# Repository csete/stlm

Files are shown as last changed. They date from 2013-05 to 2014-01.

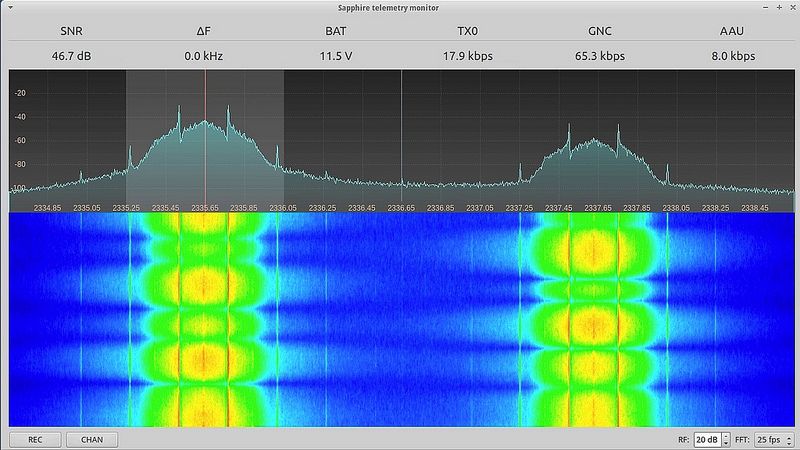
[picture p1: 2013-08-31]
doc/src/images/telemetry_monitor.jpg

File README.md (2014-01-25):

Sapphire Telemetry System
-------------------------

This repository contains the hardware and software for the Sapphire Telemetry System originally built for Copenhagen Suborbitals for their Sapphire test flight (mission video: http://www.youtube.com/watch?v=kcF5xNrb3HA).

See how the downlink performed during the test flight where the motion cause very strong fading: http://www.youtube.com/watch?v=QEViCPNmkhM

Some photos are available on Flickr: http://www.flickr.com/photos/csete/sets/72157633313520450/

The telemetry system consists of a 2.4 GHz transmitter built around the ADF7242 and a receiver built around a USRP1 with GNU Radio SDR software.

The project repository is organized in the following subdirectories:

* transmitter -- transmitter design files, including complete Eagle project and firmware source code
* receiver -- receiver design files organized as follows:
  * decoder -- The data data decoder application
  * strx -- The main GNU Radio application that acts as the software receiver
  * strx-mon -- Qt-based remote control and monitoring application for strx
  * hardware -- data sheets of varous hardware component (USRP, LNB, etc.)
* doc -- main project documentation written in asciidoc
* system -- some additional system level documentation (should also be avaialble via doc)

License and Copyright
---------------------

The transmitter is Copyright 2013 by Peter Scott, OZ2ABA.

The receiver is Copyright 2013 by Peter Scott, OZ2ABA, and Alexandru Csete, OZ9AEC.

The Viterbi decoder is Copyright Phil Karn, KA9Q,

Both the transmitter and the receiver are licensed under GNU General Public License version 3. For the transmitter other licenses can be negotiated.

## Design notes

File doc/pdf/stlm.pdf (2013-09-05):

Sapphire Telemetry System | i

# Sapphire Telemetry System

Sapphire Telemetry System | ii

REVISION HISTORY

NUMBER | DATE | DESCRIPTION | NAME
1.1 | September 2013 | | A

Sapphire Telemetry System | iii

## Contents

1 Overview | 1
2 Telemetry transmitter | 3
3 Telemetry receiver | 3
4 Packet format and bitrate budget | 11
5 Forward error correction | 13
6 Glossary | 13

Sapphire Telemetry System | 1 / 14

## 1 Overview

The Sapphire Telemetry System is a telemetry downlink system for the Sapphire test rocket by Copenhagen Suborbitals. Its purpose is to support downlink of high rate telemetry from the GNC and AAU units allowing detailed analysis of the flight.

Figure 1 shows the telemetry downlink system in context of the complete data infrastructure during the Sapphire mission. Figure 2 shows an overview of the telemetry system itself.

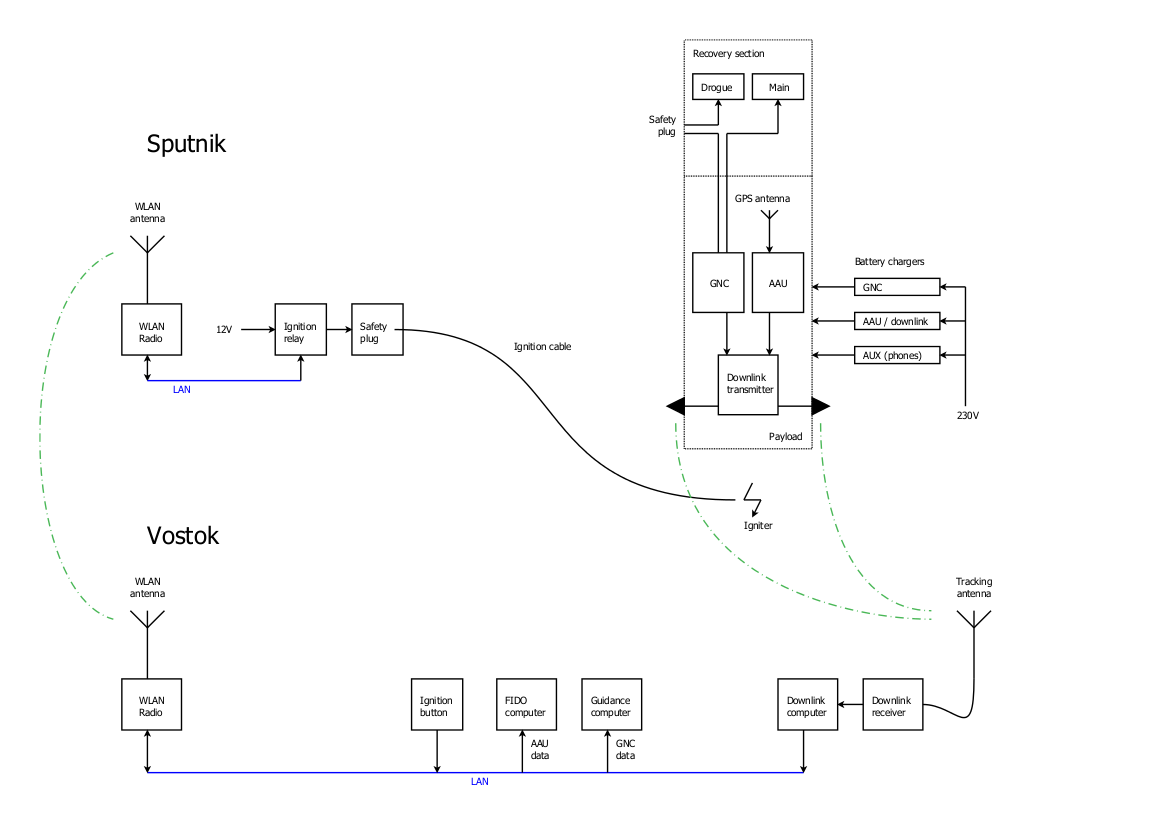
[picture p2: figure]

Figure 1: Sapphire data infrastructure

The telemetry system is based on a design originally created for the Euroluna Romit 2 cubesat and has the following character-istics:

- Two downlink channels working simultaneously.
- Works in the 13 cm amateur / ISM band.
- 1 watt RF output per channel (adjustable in firmware)
- Up to 2 Mbps bit rate per channel (including all headers, FEC, etc.)
- GFSK modulation
- CRC and FEC (rate 1/2)

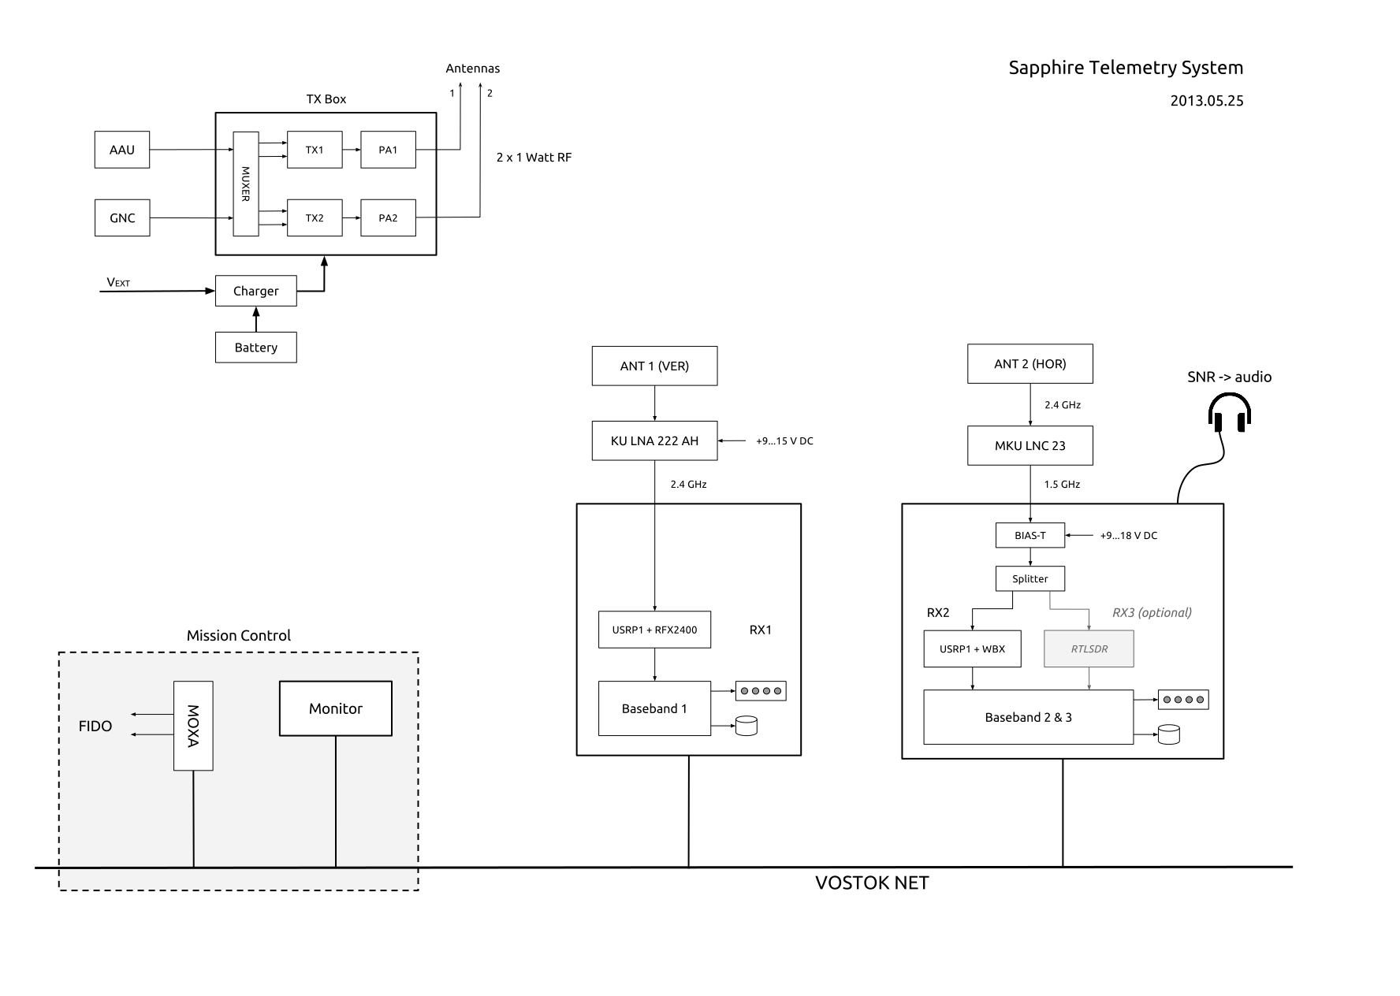
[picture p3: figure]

Figure 2: Telemetry system overview

The telemetry system contains the following components:

Transmitter
The transmitter is based on the ADF7242 transceiver chip running in raw mode. The digital data interface to the payload goes through a PIC24, which is responsible for converting the potentially variable rate data to fixed rate. The transmitter is described in more details in Section 2.

Receiver
The receiver is a software defined radio using USRP hardware and GNU Radio based software receiver. It runs on a Linux PC and delivers the telemetry data via Ethernet or RS232 interface. The receiver is set up to run autonomously and does not require any user intervention; however, key parameters are exported via a control port interface. This allows remote clients to connect to the receiver, monitor the system performance, and modify some key parameters. The receiver is described in details in Section 3.

Control panel
The monitoring and control panel is a client that connects to the receiver and displays system performance (spectrum, SNR, data and error rates, etc.) to mission control crew. It also allows modifying some basic settings in the receiver chain such as frequency, active channel, recording on/off, etc. The control panel is described in more details together with the receiver in Section 3.

Tracking tower
An AZ/EL mount built specifically for tracking fast flying objects. It can carry many antennas of different shapes and sizes as long as the construction stays balanced. For the Sapphire mission it carries two 2.4 GHz yagi antennas, one vertically and horizontally polarized. Each antenna is connected to a receiver that receives both downlink channels; however, only one channel of the horizontal receiver is monitored in real time. The other channels are recorded for reference. The tracking tower has been described in TBD.

In addition to the unit documentation listed above, following system level documentation exists:

Packet format
Describes the packet format used by the telemetry system, see Section 4.

Forward error correction
Describes the error correction code used by the system, see Section 5.

## 2 Telemetry transmitter

The transmitter is based around the ADF7242 FSK transceiver chip by Analog Devices. The transceiver is used in raw FSK mode as opposed to any of the pre-programmed modes in the chip. Raw FSK mode allows up to 2 Mbps data rate.

Figure 3: Functional diagram of the telemetry transmitter.

The transmitter is connected to the GNC and AAU unit using a serial interface. This interface is provided by a PIC24 microcon-troller which is in charge of all the data handling, including preparing the packets, calculating CRC and adding FEC. Moreover, the PIC24 is also responsible for configuring and controlling the ADF7242 transceiver chip.

For the Sapphire mission we were using 250 kbps bit rate with rate 1/2 FEC, i.e. 125 kbps data throughput. The 125 kbps data includes packet headers and other bookkeeping data. See Section 4 for details about the packet format.

The ADF7242 transmitter is running in GFSK mode. This eliminates the minimum shift restriction of FSK and reduces the occu-pied bandwidth (the transmitter uses 260 kHz shift in our case). On the other hand this also introduces inter-symbol interference that must be compensated for at the receiver end.

The ADF7242 transceiver chip is followed by a low pass filter, an ABA-54563 buffer amplifier and finally an ALM-31222 power amplifier capable of delivering 1W RF into the antenna.

## 3 Telemetry receiver

The Sapphire telemetry receiver is based on a Universal Software Radio Peripheral (USRP) hardware from Ettus Research and the GNU Radio software defined radio framework.

As indicated on Figure 2 in Section 1 we designed the system to use three receiver chains running parallel. One for receiving each telemetry channel using a USRP and a third one for testing and RTL-SDR receiver. Due to time constraints, we ended up using one USRP-based receiver for real time reception and one USRP-based receiver for recording the I/Q data to disk. The RTL-SDR experiment was not performed.

Figure 4 below shows an overview of the receiver used for real time reception.

Figure 4: Sapphire telemetry receiver

It uses an MKU LNC 23 down-converter from Kuhne Electronic, a USRP1 equipped with a WBX transceiver daughter card and connected to a PC running software receiver and data decoder. Each of these components are described in the following sections.

### 3.1 MKU LNC 23 down-converter

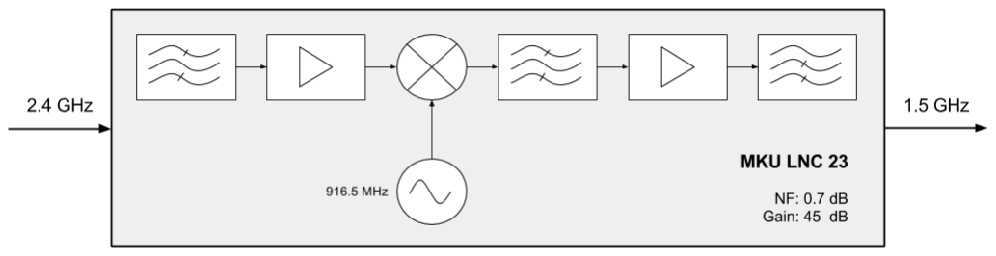
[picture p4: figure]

Figure 5: Kuhne MKU LNC 23 down-converter

The MKU LNC 23 (http://www.kuhne-electronic.de/en/products/down-converters/mku-lnc-23.html) down-converter from Kuhne Electronic (http://www.kuhne-electronic.de/startseite.html) is mounted directly on the antenna and connected using a very short coaxial cable. This gives the primary receiver chain a low noise figure and provides sufficient gain to run a long coax cable down to the receiver, which is located below deck.

The down-converter has built-in bias tee and is supplied through the coax. The supply voltage is injected into the coax using a bias tee at the USRP end below the deck.

### 3.2 USRP with WBX front end

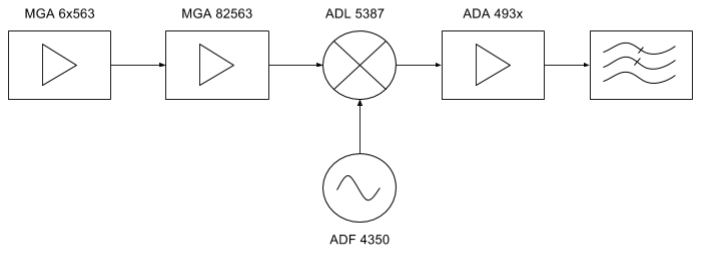
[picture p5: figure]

Figure 6: WBX receiver

The WBX transceiver board covers 50 MHz to 2.2 GHz and it has one of the best performing receivers for the USRPs. Figure 6 shows a high level diagram of the receiver part.

The board has two amplifier stages (MGA62563 and MGA82563) followed by the ADL5387 quadrature demodulator. The analog I/Q goes through an ADC driver and an anti alias filter with cut-off at around 50 MHz before it is routed to the ADC on the USRP main board.

Figure 7: USRP1 receiver

The ADC on the USRP1 runs at 64 MHz and could theoretically provide 64 MHz of bandwidth. However, since the USRP1 is connected to the host PC through USB2, the usable real-time bandwidth is limited to 8 MHz at 16 bit resolution. To that end, the ADC is followed by an FPGA running a digital down converter (DDC) providing a means to convert the 64 MHz to a lower rate. The USRP1 supports a wide variety of sample rates between 250 kHz and 8 MHz. For the Sapphire mission we have been using 4 MHz bandwidth allowing us to monitor both transmitters at the same time.

Schematics of the USRP1 and the WBX RF board are included in the receiver/hardware/ (https://github.com/csete/stlm/tree/master/receiver/hardware) directory.

### 3.3 Software receiver

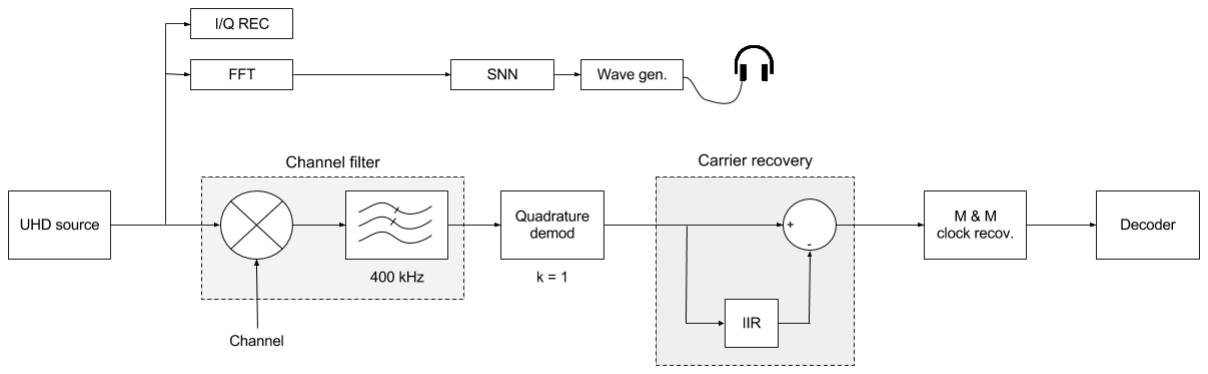
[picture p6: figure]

Figure 8: GNU Radio software receiver

The software receiver is a C++ application built using the GNU Radio SDR framework. The receiver uses both DSP blocks and the run-time framework provided by GNU Radio. In addition to that, the telemetry receiver also takes advantage of the control port interfaces, which is one of the latest additions to GNU Radio.

Most of the signal processing is executed by the GNU Radio scheduler and runs within that context. There are a few exceptions, namely the FFT block and the SNN calculations. These blocks are run in a separate boost thread scheduled periodically at 25-50 Hz. Since these are user interface related processing, there is no need to run them at higher rates.

### 3.3.1 Signal processing blocks

UHD source

The UHD source block provides the interface to the USRP hardware. We chose to use gr-uhd as input source for the Sapphire mission because we only needed USRP interface. A gr-osmosdr source could be used instead with minor modifications.

FFT

This blocks performs complex FFT on the input spectrum. The FFT is performed in three stages: 1. The first stage is a block in the GNU Radio flow graph that stores the incoming samples in a circular buffer. 2. The second stage fetches the last N samples from the circular buffer (N is the FFT size), performs the FFT calculations and prepares the data for presentation (scales to dBFS and translates the spectrum). This function is executed periodically at 25-50 Hz outside of the GNU Radio scheduling. 3. The third stage delivers the latest FFT data to external clients through the gnuradio-controlport interface.

I/Q recorder

This block is a simple file sink that dumps the complex I/Q samples to a file.

We found that it is rather problematic to save I/Q files at high rate and perform real time signal processing at the same time on the same computer. When recording is enabled, the operating system will start caching until it runs out of available RAM. Once it’s out of RAM it will start writing data to the disk periodically. The amount of data that needs to be written is huge and SDR processing is suspended during the write. Although the dropouts are very brief in duration, they are quite frequent and lead to loss of samples. Consequently, the correctly received packet rate dropped from 99% to 60%.

There are several things one can do to improve the situation:

1. Use faster hardware optimized for continuous disk I/O.
2. Get more RAM and use a RAM disk if possible. This can’t be used for long duration recordings.
3. Tune the virtual memory parameters of the kernel. We found that following parameters allowed for continuous recording on a low end Dell server:

sysctl -w vm.swappiness=0
sysctl -w vm.dirty_background_bytes=1048576 sysctl -w vm.dirty_writeback_centisecs=20 sysctl -w vm.dirty_expire_centisecs=30

The above settings pretty much disables caching and are not recommended for daily use on desktop systems. Use "vmstat 1" for monitoring how the system is caching. Documentation for the Linux kernel VM settings is available in the sysctl/vm document. (https://www.kernel.org/doc/Documentation/sysctl/vm.txt)

SNN & tracking

The SNN block calculates the (S+N)/N ratio where S stand for signal power and N for noise power in dB. The SNN is converted to an audio tone by the wave generator block and is used as an audio aid for tracking. The higher the tone the stronger the signal.

The SNN calculation is based on the FFT. Therefore, the SNN and wave generator blocks are scheduled by the same thread as the FFT processing outside of the GNU Radio main loop.

Frequency translating FIR filter

The frequency translating FIR filter has three functions:

1. Translate the spectrum so that the signal of interest is at 0 Hz.
2. Perform low pass filtering.
3. Decimate the data to a lower rate.

The frequency translation allows us to perform software-based tuning within the received spectrum. We use this functionality to select which downlink channel to decode i real time, see e.g. Figure 11.

The cut-off frequency of the low pass filter is initially set to 400 kHz but it can be adjusted during run time. The transition width is set to be equal to the cut-off frequency. Note that a 400 kHz cut-off corresponds to an 800 kHz wide channel when we are filtering at complex baseband.

The decimation factor is set to 2 so the spectrum after the filter is 2 MHz wide.

Demodulator

The transmitter uses frequency shift keying followed by a Gaussian filter to eliminate the minimum shift requirement and reduce the bandwidth. On the receiver end we can use a standard quadrature demodulator followed by a matching filter to compensate for some of the inter-symbol interference introduced by the Gaussian shaping of the signal.

The quadrature demodulator block takes a parameter, which determines the modulation factor. Sometimes it’s called sensitivity, sometimes it’s called gain — we just call it k. In an analog system k is the ratio between the quadrature rate and the maximum deviation (and reversed for the modulator). In a digital system this translates to samples per symbol assuming that the minimum shift condition is met.

For the Sapphire mission we have used k = 1, which is not optimal but sufficient thanks to the large margin we had in the link budget.

FIXME: Gaussian filter is missing in the Sapphire receiver.

Carrier recovery

Under optimal conditions the output from the quadrature demodulator will be ±1 corresponding to 0 and 1. One of these optimal conditions is that the receiver is tuned to the exact same frequency as the transmitter. In practice this is rather difficult and expensive to accomplish and it is better to tolerate slight frequency offsets.

When using frequency modulation such an offset will cause the output levels from the demodulator to shift up or down by a constant and is therefore easy to compensate. We use a single pole IIR filter to calculate the running average of the output samples and correct for the offset before sending the samples to the clock recovery block. This has the advantage of being able to correct even for variable frequency drifts.

For the Sapphire mission we used alpha = 1e-3, corresponding to a time constant 0.5 ms.

Clock recovery

Our sample rate after the channel filter is reduced to 2 Msps. With a symbol rate of 250k this gives us 8 samples per symbol to work with. However, clock skew between the transmitter and the receiver may lead to this rate being different in practice, e.g. 7.998 or 8.01. The clock recovery block helps us determine this clock skew and select the "best" sample to be sent to the decoder.

The Mueller & Muller clock recovery algorithm requires only one sample per symbol and finds the correct timing by calculating an error term using the present and the previous symbol:

en = (y’n * yn-1) - (yn * y’n-1)

where y refers to the symbol (+1 or -1) and y’ refers to the actual sample (any float).

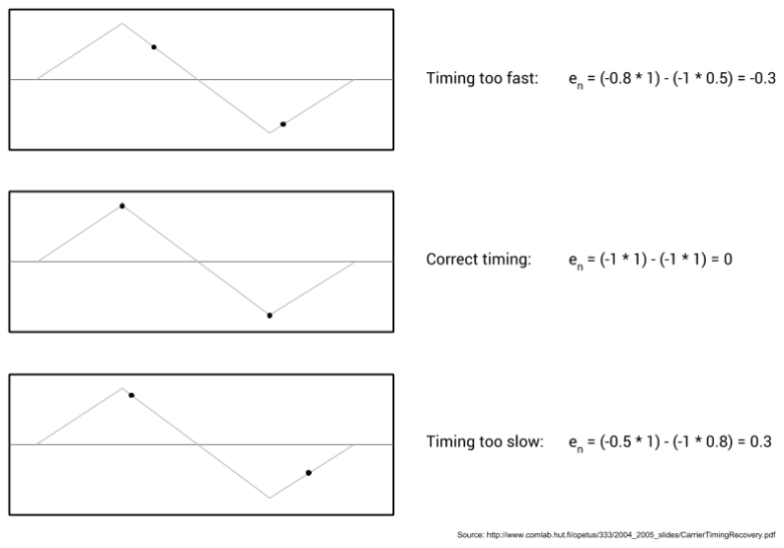
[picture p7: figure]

Figure 9: Mueller & Muller clock recovery

The Mueller & Mullerr clock recovery algorithm is sensitive to carrier offsets which is why we perform the carrier recovery described in the previous section.

### 3.3.2 Command line interface

The software receiver is a command line application with the following command line options:

alc@atlantis:~/sdr/stlm.git/receiver/build$ ./strx -h
linux; GNU C++ version 4.7.3; Boost_105300; UHD_003.005.003-140-gc099f2b5

Sapphire telemetry receiver 0.3
Command line options:
-h [ --help ] | This help message
-n [ --name ] arg | Receiver name (used for ctrlport)
-i [ --input ] arg | USRP sub device or I/Q file (use file:/path/to/file)
-a [ --ant ] arg | Select USRP antenna (e.g. RX2)
-f [ --freq ] arg | RF frequency in Hz or using G, M, k suffix
-g [ --gain ] arg | RF/IF gain in dB
-l [ --lnb ] arg | LNB LO frequency in Hz or using G, M, k suffix
-o [ --output ] arg | Output file (use stdout if omitted)
--audio arg (=none) | Audio output device (e.g. pulse, none)

### 3.4 Data decoder

Figure 10: Data decoder

The data decoder runs as a separate process

First, the decoder looks for the sync bytes that each packet begins with c.f. Figure 12 in Section 4. Once sync is obtained the decoder begins running the bytes through the Viterbi decoder. Recall that we are using convolutional FEC and all bytes in a FEC frame are encoded.

The final step in the decoding process is the packet recovery, which consists of detecting the packet boundary, checking the packet length, the CRC, extracting the packet source and finally forwarding it to the respective user.

### 3.5 Monitoring and control


Figure 11: Sapphire telemetry monitor

Monitoring and control of the receiver is carried out using the Sapphire telemetry monitor. It is a simple Qt-based application called strx-mon, which connects to the receiver and the data decoder using network sockets.

Connection to the receiver is done through the gnuradio-controlport interface. Following interfaces are implemented for the Sapphire mission:

- FFT and waterfall plot of the receiver spectrum (4 MHz).
- Change FFT rate.
- Toggle between downlink channels.
- Signal to noise ratio (SNN actually) of the selected channel.
- Show and adjust filter bandwidth.
- Show and adjust USRP gain.
- Start and stop I/Q recording.

Connection to the data decoder is done through a raw TCP connection. Whenever a character is sent over the connection, the decoder will reply with:

- Decoded AAU telemetry in bytes.
- Decoded GNC telemetry in bytes.
- Decoded transmitter telemetry in bytes.

- Current transmitter ID.
- Current battery voltage.
- Transmitter uptime.

The telemetry monitor polls the decoder periodically and translates the received status into data throughput in kilobits per second.

You can watch the Sapphire telemetry monitor i action in this YouTube video (http://www.youtube.com/watch?v=QEViCPNmkhM) showing a replay of the data downlink during the flight. The video is also a good demonstration of the telemetry system performance under harsh flight conditions (strong vibrations and tumbling).

## 4 Packet format and bitrate budget

The Sapphire telemetry is a continuous stream of packetized data. The data comes from the GNC and AAU units and packed into the frame structure described here. When neither GNC nor AAU are transmitting data, the transmitter will fill out the empty slots using own telemetry. This will ensure that the receiver can stay locked and synchronized to the signal even when there is no telemetry from the payload.

The Sapphire telemetry system uses a very simple packet format shown on the figure below:

Figure 12: The Sapphire packet structure

A packet consists of the following parts:

- A fixed length packet header (11 bytes)
- Variable length data field (up to 255 bytes)
- CRC for the data field (2 bytes)
- FEC field that applies to parts of the header (last 5 bytes), the data field and the CRC

### 4.1 Packet header

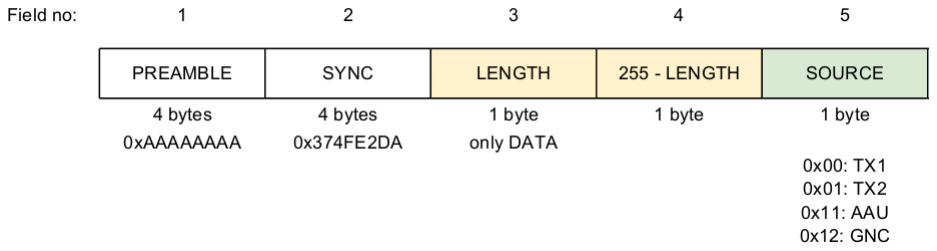
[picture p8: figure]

Figure 13: Sapphire telemetry packet header

The packet header contains the following fields:

1. A 4 byte PREAMBLE field consisting of alternating 0 and 1. The preamble is used for training the clock recovery in the receiver.
2. A 4 byte SYNC field containing the pattern 0x374FE2DA. The SYNC field is used by the correlator in the receiver to identify a packet.
3. A 1 byte LENGTH field specifying the number of bytes in the data field.
4. Another 1 byte length field but this time the "inverse" (255-LENGTH).
5. A one byte SOURCE field specifying the origin of the packet. This information is used by the data distribution system in mission control to route the packets to their respective users. Following values are valid:
- 0x00: TX1
- 0x01: TX2
- 0x11: AAU
- 0x12: GNC

### 4.2 Data field

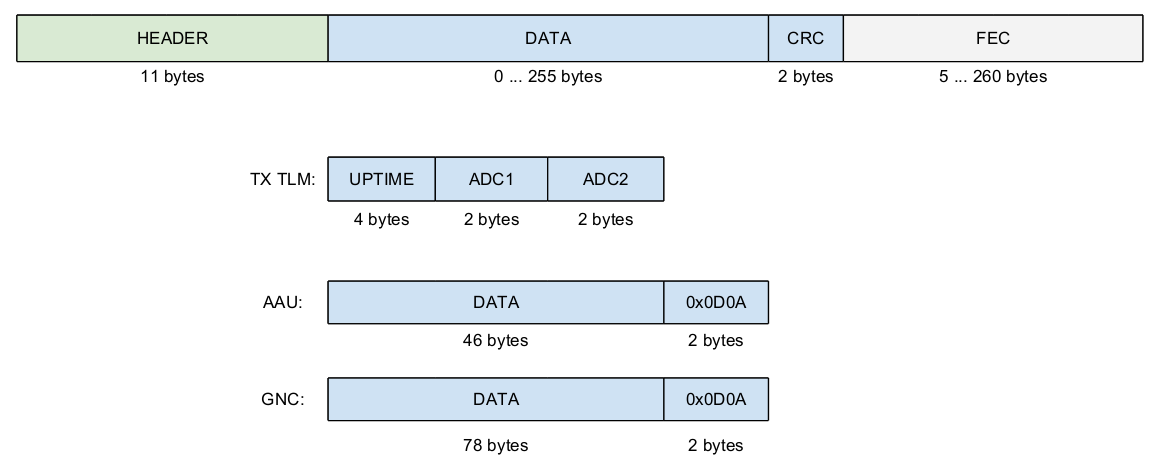
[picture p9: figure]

Figure 14: Sapphire telemetry data field

The data field contains the data as received from the payload. There are two types of payload data as indicated on the figure above. They are terminated with carriage return and linefeed characters 0x0D0A indicating packet end. The transmitter interprets this as a "flush the buffer" command even if 0x0D0A occurs inside the data. In practice this may lead to fragmentation of payload packets; however, this is not expected to cause any problems at the receiving end.

A third type of packet contains telemetry from the transmitter itself. These packets are used to fill out empty slots that are not used by the payload. See Section 4.5 for details.

The transmitter packets contain the transmitter uptime in 1/10th of a second and two raw ADC readings corresponding to the supply voltage and the temperature inside the PIC24.

### 4.3 CRC field

A 16-bit CRC is added to each packet in order to allow verifying correct packet reception. The CRC is generated using the programmable CRC generator in the PIC24 using the polynomial x¹⁶+x¹²+x⁵+1.

### 4.4 FEC field

Figure 15: FEC frame

FEC is applied to all fields except the PREAMBLE and SYNC fields in the header. A FEC frame is thus 5 + N bytes long, where N is the length of the data field. Since we are using convolutional code we do not really have separate data and FEC fields as suggested by the figure. Instead, each byte is encoded as soon as it arrives and the coded data is put into the output buffer.

### 4.5 Downlink budget

In the present configuration we have 250 kbps at our disposal. We apply rate 1/2 FEC to the data, thus we have 125 kbps at our disposal. Table 1 below shows the downlink budget under these circumstances. As can be seen from the table, almost half of the traffic is transmitter telemetry to fill out empty slots, thus there is plenty of room for future increase in data rate.

Table 1: Bitrate budget

Source | Packet size [bytes/pkt]
Packet
overhead
[bytes/pkt]

Packet
length
[bits/pkt]

Packet rate
[pkt/sec]

Bitrate [bps]

GNC | 80 | 12 | 736 | 102.25 | 75255.62
AAU | 48 | 12 | 480 | 20.00 | 9600.00
TX | 10 | 12 | 176 | 198.00 | 34848.00
Total | | | | | 119.70 k

## 5 Forward error correction

To be written

As writen in the Packet Format section, we use both CRC and rate 1/2 convolutional error correction code. While the convolutional code is used to correct bit errors in the received data, the CRC is used to verify that the received data is correct.

## 6 Glossary

AAU | Autonomous Abort Unit
ADC | Analog to digital converter
AZ | Azimuth
CRC | Cyclic redundancy check

EL | Elevation
FEC | Forward error correction
FSK | Frequency shift keying
GNC | Guidance, navigation and control
ISM | Unlicensed frequency bands used by industrial, scientific and medical devices
RF | Radio frequency
SDR | Software defined radio
SNN | Signal+noise to noise ratio
SNR | Signal to noise ratio
USRP | Universal Software Radio Peripheral

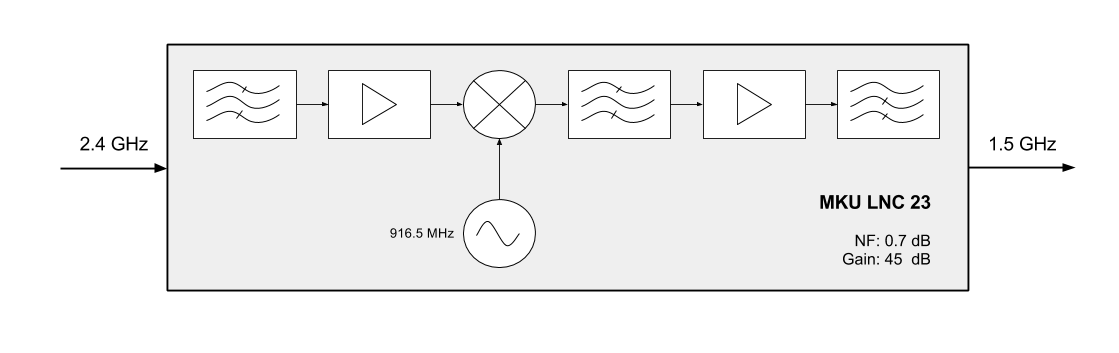
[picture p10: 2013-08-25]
doc/src/images/mku_lnc_23.png

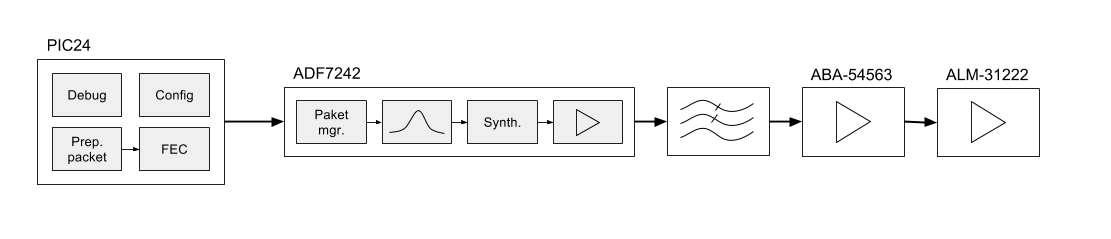
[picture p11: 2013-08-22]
doc/src/images/transmitter.png

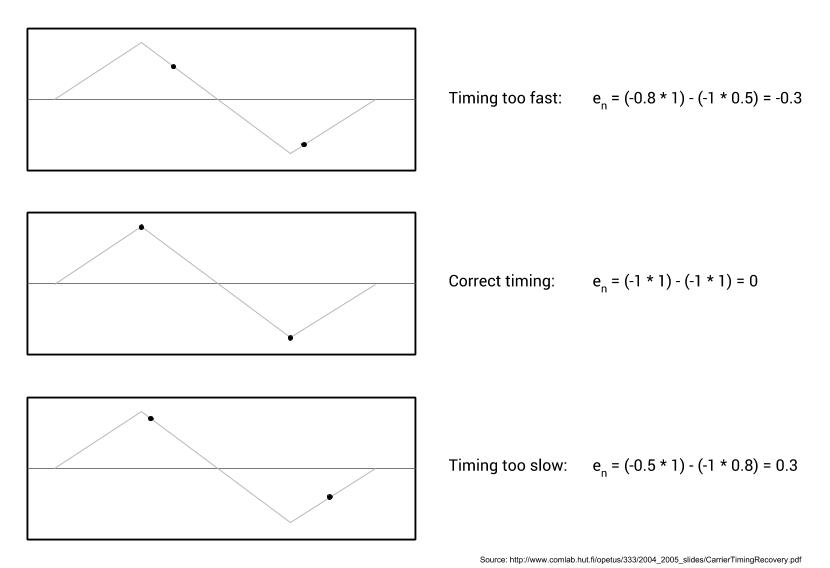
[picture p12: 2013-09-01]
doc/src/images/mm_clock_recovery.png

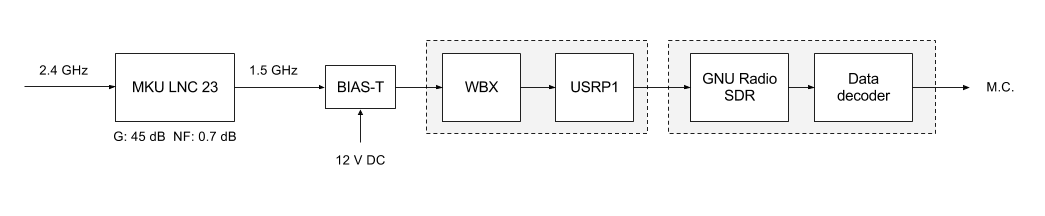
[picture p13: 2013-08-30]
doc/src/images/telemetry_receiver.png

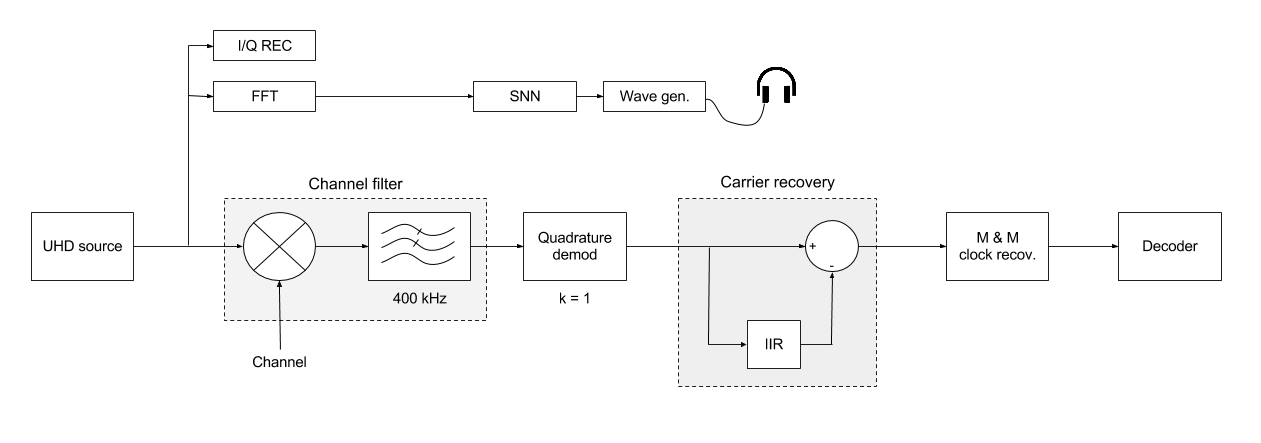
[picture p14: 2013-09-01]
doc/src/images/software_receiver.png

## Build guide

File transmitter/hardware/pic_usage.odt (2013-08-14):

Usage of PIC hardware resources

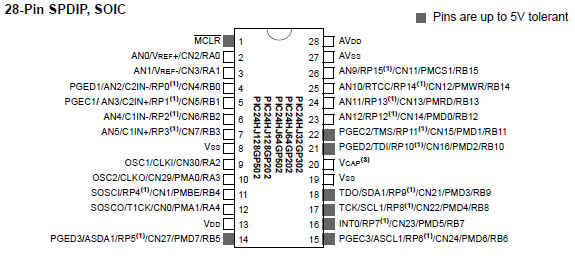
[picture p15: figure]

PIC Pin mapping

Description | PIC24 pin | | PIC24 pin | Description
-MCLR / ICSP Reset | 1 | | 28 | AVDD – 3.3 volt
RA0 - DS18 temp | 2 | | 27 | AVSS – GND
RA1 - -CS | 3 | | 26 | AN9 - Vbatt
RP0 – MOSI | 4 | | 25
RP1 – SCLK | 5 | | 24 | RP13 – RX2
RP2 – MISO | 6 | | 23 | RP12 – TX2
RP3 – TRCLK | 7 | | 22 | PGEC2 – ICSP Clock
Vss – GND | 8 | | 21 | PGED2 – ICSP Data
RA2 - LED1 | 9 | | 20 | Vcap
RA3 - LED2 | 10 | | 19 | Vss – GND
RP4 – DT | 11 | | 18 | SDA1 - I2C
RA4 - -PAenable | 12 | | 17 | SCL1 - I2C
Vdd – 3.3 volt | 13 | | 16 | RP7 - RX1
RP5 – DR | 14 | | 15 | RP6 - TX1

ADF7242 digital IO pins

Seen from top to bottom as they approach the PIC:

Pin # | Name | Function
24 | -CS | SPI Chip Select
23 | MOSI | SPI Serial Input
22 | SCLK | SPI Clock Input
21 | MISO | SPI Serial Output
19 | TRCLK_CKO_GP3 | SPORT Bit Clock Output
17 | DT_GP1 | SPORT Transmit Data Input
16 | DR_GP0 | SPORT Receive Data Output

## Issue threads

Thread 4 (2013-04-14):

LED indicator

csete, 2013-04-14:
We need a hardware indicator that can tell us the status of the complete telemetry chain. The idea is to have 4 (maybe 5) LEDs indicating the following:
- PWR: Goes on as soon as device is powered.
- RX: Goes on as soon as SNR is above threshold, which is TBC.
- SYNC: Goes on when the correlator detects valid packets.
- DATA: Goes on when the correlator detects packets from GNC or AAU.

Optionally:
- NET: Goes on when correlator successfully delivers packets to FIDO.

The easiest and fastest is probably to use an Arduino driven over usb-serial.

This works only for a single receiver and correlator, however, if the two-channel diversity is handled by the correlator, this indicator will work without modifications.

Closed 2017-03-28.

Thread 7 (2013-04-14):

Control panel

csete, 2013-04-14:
The control panel is a graphical interface to the telemetry receiver. It's purpose is to monitor the performance of the telemetry chain. The control panel does not perform any computationally intensive tasks but it must be able to perform basic graphics very efficiently.

The control panel is a client to the control port interface exposed by the telemetry receiver.

Expected hardware configuration:
- Raspberry Pi running Raspbian wheezy 2013-02-09.
- Lilliput 5D-ii/O/P 7" HDMI field monitor.
- An extension box that adds a few buttons and knobs for function shortcuts.

The control panel will organize the available parameters according to the following operating modes:
1. Mission
2. Engineering
3. Debug (TBC)

Closed 2017-03-28.

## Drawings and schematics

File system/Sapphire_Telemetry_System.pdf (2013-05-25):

## Sapphire Telemetry System

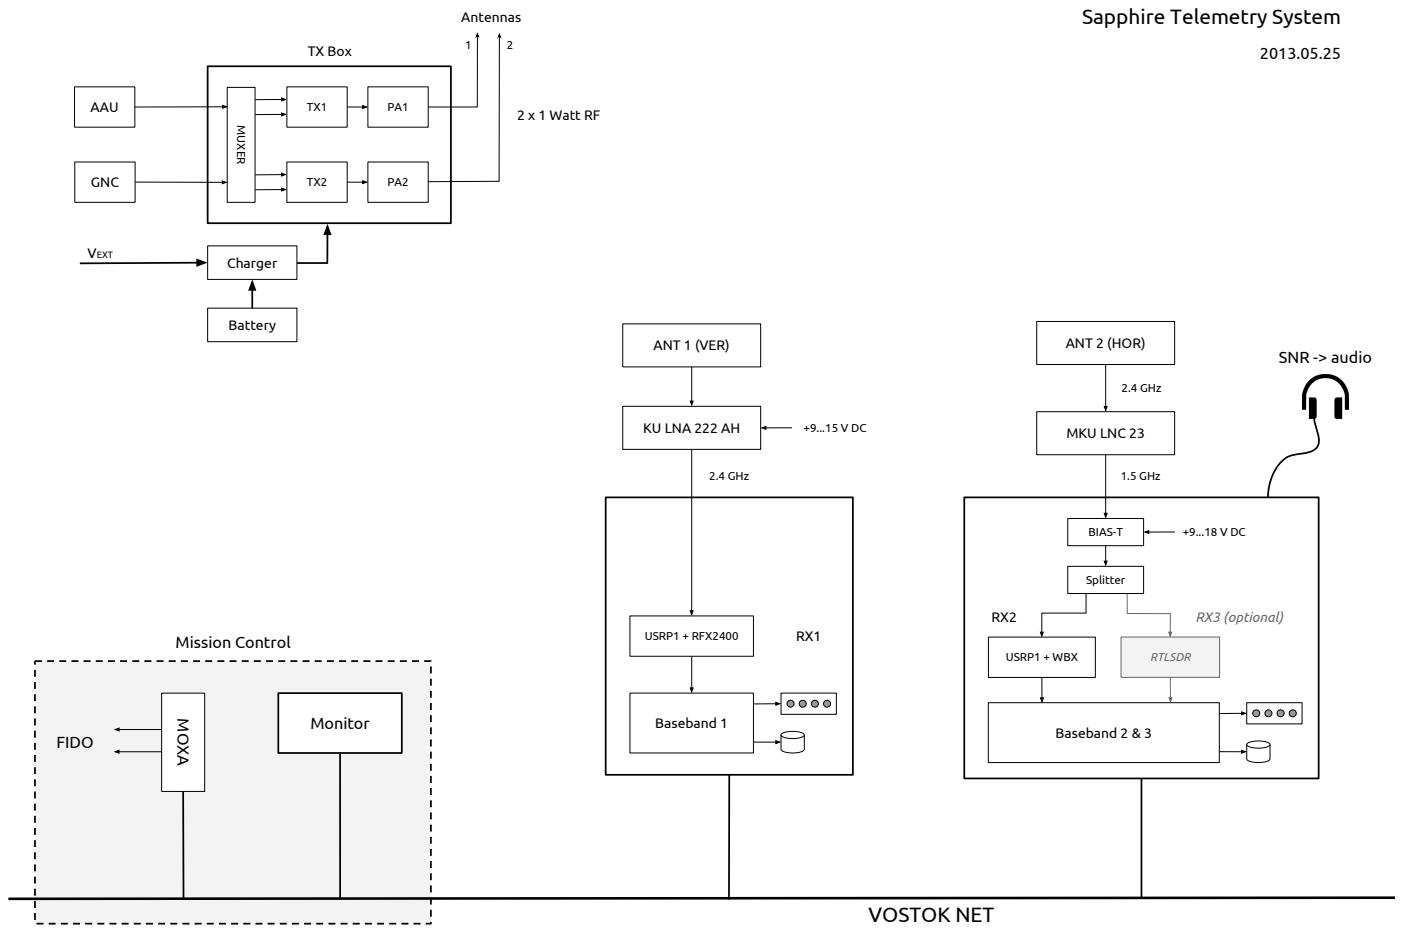
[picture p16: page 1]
AAU; GNC; MUXER; TX Box; Antennas; Charger; Battery; USRP1 + RFX2400; Baseband 1; RTLSDR; Baseband 2 & 3; RX3 (optional); Splitter; USRP1 + WBX; BIAS-T; MKU LNC 23; 1.5 GHz; 2.4 GHz; ANT 1 (VER); ANT 2 (HOR); VOSTOK NET; MOXA; Monitor; Mission Control; FIDO; KU LNA 222 AH; 2 x 1 Watt RF; VEXT; SNR -> audio

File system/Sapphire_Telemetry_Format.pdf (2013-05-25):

Field no: | 1 | 2 | 3 | 4 | 5 | 6 | 7 | 8
| PREAMBLE | SYNC | LENGTH | 255 - LENGTH | SOURCE | DATA | CRC | FEC
| 4 bytes | 4 bytes | 1 byte | 1 byte | 1 byte | up to 255 bytes | 2 bytes | 5 + LENGTH bytes
| 0xAAAAAAAA | 0x374FE2DA | only DATA | | | | | Applies to fields 3 to 7
| | | | | 0x00: TX1 0x01: TX2 0x11: AAU 0x12: GNC
TX TLM: | UPTIME | ADC1 | ADC2
| 4 bytes | 2 bytes | 2 bytes
AAU: | DATA | 0x0D0A
| 46 bytes | 2 bytes
GNC: | DATA | 0x0D0A
| 78 bytes | 2 bytes

Sapphire Telemetry Format - Overview

## Bitrate budget

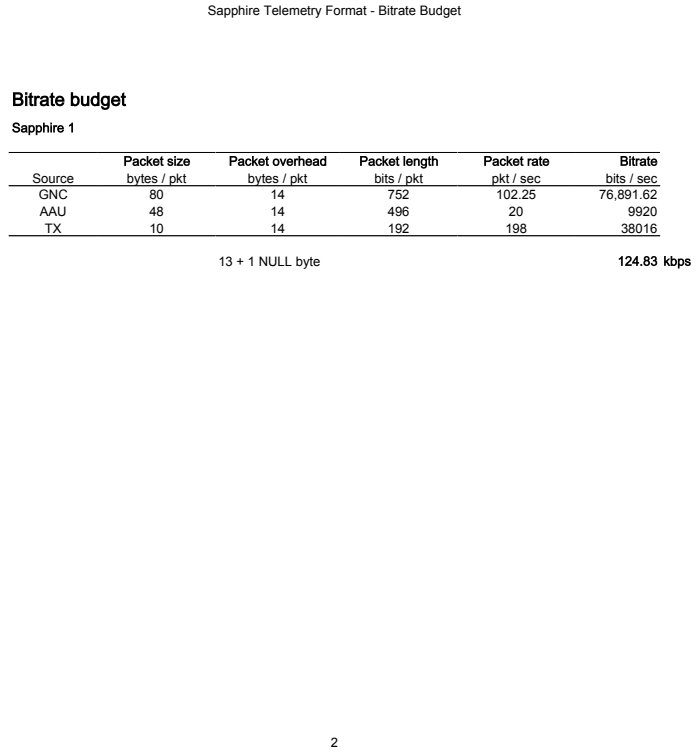
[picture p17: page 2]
13 + 1 NULL byte; kbps

Sapphire Telemetry Format - Bitrate Budget

Sapphire 1

Packet size | Packet overhead | Packet length | Packet rate | Bitrate

Source | bytes / pkt | bytes / pkt | bits / pkt | pkt / sec | bits / sec
GNC | 80 | 14 | 752 | 102.25 | 76,891.62
AAU | 48 | 14 | 496 | 20 | 9920
TX | 10 | 14 | 192 | 198 | 38016

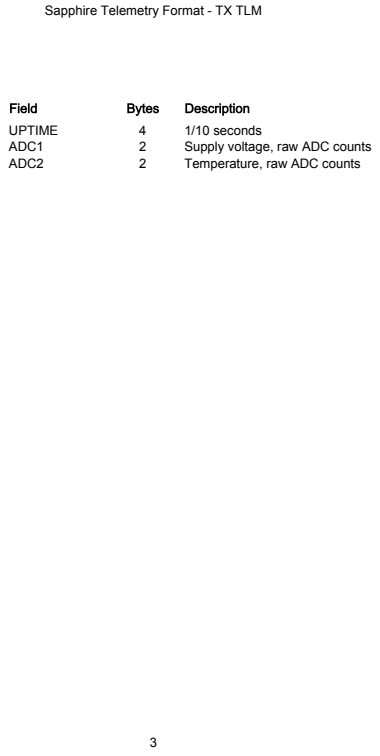
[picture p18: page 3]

Sapphire Telemetry Format - TX TLM

Field | Bytes | Description
UPTIME | 4 | 1/10 seconds
ADC1 | 2 | Supply voltage, raw ADC counts
ADC2 | 2 | Temperature, raw ADC counts

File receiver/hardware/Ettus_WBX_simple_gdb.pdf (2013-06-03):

# TX/RX

# TX_CONN6V_TX:1

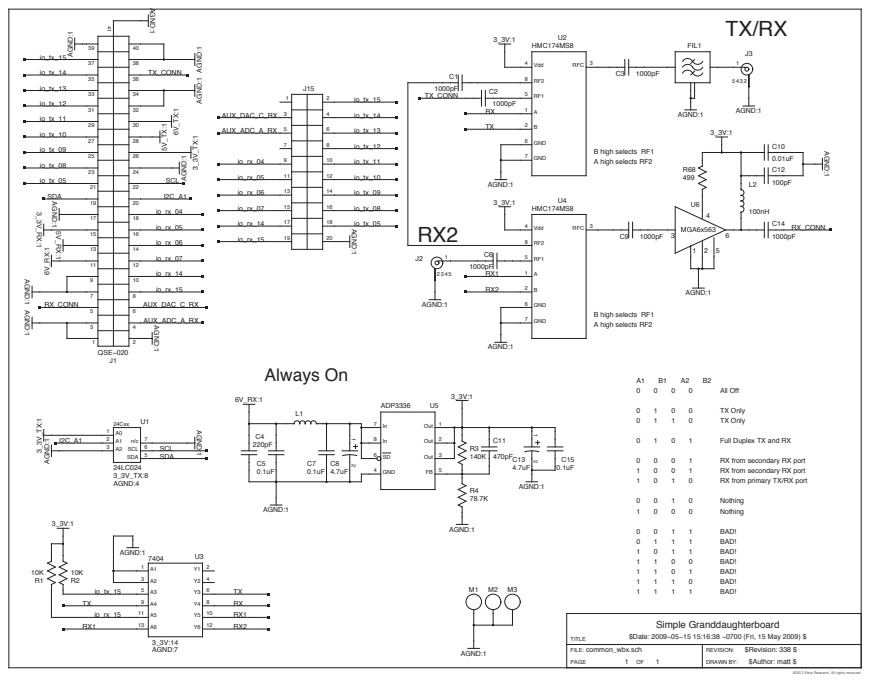
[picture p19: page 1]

©2012 Ettus Research. All rights reserved.

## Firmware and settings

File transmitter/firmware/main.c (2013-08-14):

/********************************************************************************
*																				*
*	Copenhagen Suborbitals														*
*																				*
*	2.3 GHz Telemetry Transmitter												*
*																				*
*	Version:	1.1.1															*
*	Supports hardware version 1.0 and 1.1										*
*																				*
********************************************************************************/

#define HWVERSION	11		/* Alias for 1.1 */


#include <xc.h>
#include <stdint.h>
#include <string.h>

/* Setup clock speed. */
#pragma config FNOSC = FRCPLL
#pragma config ICS = PGD2				/* Debugger is connected to PGC2/PGD2 pins. */
#pragma config FWDTEN = OFF				/* Disable watchdog. */
#pragma config OSCIOFNC = ON			/* Use Pin-10 as regular output. */

/* IO Pin layout. */

#if HWVERSION == 10
#define LED_1				LATBbits.LATB15
#define LED_2				LATBbits.LATB14
#define LED_1_TRIS			TRISBbits.TRISB15
#define LED_2_TRIS			TRISBbits.TRISB14

#define ADF_CS				LATAbits.LATA1		/* RA1  <= CS pin for the ADF. */
#define ADF_CS_TRIS			TRISAbits.TRISA1	/* --///-- */
#define ADF_SCK				PORTBbits.RB1		/* RP1/RB1 */
#define ADF_SCK_TRIS		TRISBbits.TRISB1	/* --///-- */
#define ADF_SDO_TRIS		TRISBbits.TRISB0	/* RP0/RB0 */
#define ADF_SDI				PORTBbits.RB2		/* RP2/RB2 */
#define ADF_SDI_TRIS		TRISBbits.TRISB2	/* --///-- */
#define ADF_SPORT_CLK_TRIS	TRISBbits.TRISB3	/* RP3/RB3 */
#define ADF_SPORT_SDO_TRIS	TRISBbits.TRISB4	/* RP4/RB4 */
#define ADF_SPORT_SDI_TRIS	TRISBbits.TRISB5	/* RP5/RB5 */

#define RX1_IN				PORTBbits.RB9
#define RX2_IN				PORTBbits.RB13

#elif HWVERSION == 11
#define LED_1				LATAbits.LATA2
#define LED_2				LATAbits.LATA3
#define LED_1_TRIS			TRISAbits.TRISA2
#define LED_2_TRIS			TRISAbits.TRISA3

#define PA_EN				LATAbits.LATA4
#define PA_EN_TRIS			TRISAbits.TRISA4

#define ADF_CS				LATAbits.LATA1		/* RA1  <= CS pin for the ADF. */
#define ADF_CS_TRIS			TRISAbits.TRISA1	/* --///-- */
#define ADF_SCK				PORTBbits.RB1		/* RP1/RB1 */
#define ADF_SCK_TRIS		TRISBbits.TRISB1	/* --///-- */
#define ADF_SDO_TRIS		TRISBbits.TRISB0	/* RP0/RB0 */
#define ADF_SDI				PORTBbits.RB2		/* RP2/RB2 */
#define ADF_SDI_TRIS		TRISBbits.TRISB2	/* --///-- */
#define ADF_SPORT_CLK_TRIS	TRISBbits.TRISB3	/* RP3/RB3 */
#define ADF_SPORT_SDO_TRIS	TRISBbits.TRISB4	/* RP4/RB4 */
#define ADF_SPORT_SDI_TRIS	TRISBbits.TRISB5	/* RP5/RB5 */

#define RX1_IN				PORTBbits.RB7
#define RX2_IN				PORTBbits.RB13

#else
#error "Unknown hardware version."
#endif


/* Define the clocking scalers. */
#define C_FOSC 			7370000		/* Frequency of internal FRC oscillator. */

#if 0
#define C_FRCDIV		1			/* No additional scaling of FRC. */
#define C_FRCDIV_		0

#define C_PLLPRE		2			/* PLL Prescaler: 1:2 */
#define C_PLLPRE_		0

#define C_PLLDIV		43			/* PLL loopback divider 43. */
#define C_PLLDIV_		C_PLLDIV-2

#define C_PLLPOST		2			/* PLL Postscaler: 1:2 */
#define C_PLLPOST_		0

#define C_DOZE			1			/* DOZE prescaler: 1:1 */
#define C_DOZE_			0
#else
#define C_FRCDIV		1			/* No additional scaling of FRC. */
#define C_FRCDIV_		0

#define C_PLLPRE		7			/* PLL Prescaler: 1:7 */
#define C_PLLPRE_		(C_PLLPRE-2)

#define C_PLLDIV		152			/* PLL loopback divider 152. */
#define C_PLLDIV_		(C_PLLDIV-2)

#define C_PLLPOST		2			/* PLL Postscaler: 1:2 */
#define C_PLLPOST_		0

#define C_DOZE			1			/* DOZE prescaler: 1:1 */
#define C_DOZE_			0
#endif

#define C_FCY (C_FOSC * C_PLLDIV / (C_FRCDIV * C_PLLPRE * C_PLLPOST * 2))



/* Global variables. */
uint32_t		uptime = 0;			/* Uptime counter - in 1/10 seconds intervals. */
unsigned char	update_flag = 0;	/* Timer update flag - used for slow updates in the main loop. */

unsigned int	debug;
unsigned char	pa_level;
unsigned char	pa_enable = 0;		/* By default enable the PA module. */
unsigned int	id_no = 0;
unsigned int	rx1_idle;
unsigned int	rx2_idle;


/****************************************************************
*																*
*	TIMER1 services - used for time keeping.					*
*																*
****************************************************************/

static void init_timer1 (void)
{
	T1CONbits.TON = 0;			/* Timer disabled. */
	T1CONbits.TCS = 0;			/* Use Internal clock (Fcy). */
	T1CONbits.TGATE = 0;		/* Disable gated Timer mode. */
	T1CONbits.TCKPS = 3;		/* Use 1:256 prescaler. */
	T1CONbits.TSIDL = 0;		/* Continue in Idle mode. */
	TMR1 = 0x00;				/* Clear the timer register. */
	PR1 = C_FCY / (256 * 10);	/* Set the period register to 10 periods / second. */

	IPC0bits.T1IP = 0x01;		/* Priority level 1. */
	IFS0bits.T1IF = 0;			/* Clear any pending interrupts. */
	IEC0bits.T1IE = 1;			/* Enable interrupts. */

	T1CONbits.TON = 1;			/* Start the timer. */
}

void __attribute__((__interrupt__,__auto_psv__)) _T1Interrupt (void)
{
	uptime++;					/* Increment the uptime counter. */
	update_flag = 1;			/* Set the update flag so the main loop can do maintenance. */

	IFS0bits.T1IF = 0;			/* Clear the interrupt flag again. */
}



/****************************************************************
*																*
*	SPI1 services - used for commanding the ADF.				*
*																*
****************************************************************/

/* @brief  Initialize SPI1 for commanding the ADF
 */
static void init_spi1 (void)
{
	unsigned char	dummy;

	SPI1STATbits.SPIEN = 0;		/* Disable the SPI1 module. */
	SPI1STATbits.SPISIDL = 0;	/* Continue when in idle mode. */
	SPI1STATbits.SPIROV = 0;	/* No receiver overflow yet. */

	SPI1CON1bits.MODE16 = 0;	/* 8-bit mode. */
	SPI1CON1bits.MSTEN = 1;		/* SPI1 operates in master mode (drives the clock). */
	SPI1CON1bits.DISSCK = 0;	/* SPI clock is enabled. */
	SPI1CON1bits.DISSDO = 0;	/* SDO pin controlled by module. */
	SPI1CON1bits.SMP = 0;		/* Input data sampled at middle of data output time. */
	SPI1CON1bits.CKP = 0;		/* Polarity: low is inactive. */
	SPI1CON1bits.CKE = 1;		/* Output change when clock goes from idle to active. */
	SPI1CON1bits.SSEN = 0;		/* SS is controlled by software. */
	SPI1CON1bits.SPRE = 0;		/* Secondary prescaler 8:1 */
	SPI1CON1bits.PPRE = 0;		/* Primary prescaler 64:1 */

	SPI1CON2bits.FRMEN = 0;		/* No framed mode (done in software). */

	ADF_CS = 1;					/* Set the CS pin high (inactive). */
	ADF_CS_TRIS = 0;			/* Enable the CS pin as an output. */

	ADF_SCK_TRIS = 0;			/* Enable the SCK pin as an output. */
	ADF_SDO_TRIS = 0;			/* Enable the SDO pin as an output. */
	ADF_SDI_TRIS = 1;			/* Enable the SDI pin as an input. */

	IPC2bits.SPI1IP = 0x00;		/* Priviledge level 0 => disabled. */
	IEC0bits.SPI1IE = 0;		/* Disable interrupt here too. */

	SPI1BUF = 0xFF;				/* Load a NOP byte into the tx register. */
	SPI1STATbits.SPIEN = 1;		/* Enable the SPI1 module. */

	dummy = SPI1BUF;			/* Flush the SPI1 buffers. */
}


/** @brief  Read the status word from the tranceiver chip.
 *
 * @return: the status word from the chip.
 */
unsigned char adf_read_status (void)
{
	unsigned char	ret;

	/* Select the chip by lowering the CS pin. */
	ADF_CS = 0;

	/* Then wait for the SPI ready status bit to go high. */
	Nop ();
	Nop ();
	while (ADF_SDI == 0);

	/* Send a SPI_NOP byte. */
	SPI1BUF = 0xFF;

	/* Wait for the BufferFull bit to be set (end of transmission). */
	while (SPI1STATbits.SPIRBF == 0);
	ret = SPI1BUF;

	/* Send one more SPI_NOP byte. */
	SPI1BUF = 0xFF;

	/* Wait for the BufferFull bit to be set (end of transmission). */
	while (SPI1STATbits.SPIRBF == 0);
	ret = SPI1BUF;

	/* Wait for the clock bit to drop low again. */
	while (ADF_SCK == 1);

	/* Unselect the transceifer chip by raising the CS pin. */
	ADF_CS = 1;	

	return ret;			/* Return the status word. */
}


/** @brief  Wait for the command queue in the ADF to be ready.
 *
 * @return: The status word from the ADF.
 */
unsigned char adf_wait_ready (void)
{
	unsigned char	ret;

	do {
		ret = adf_read_status ();
	} while ((ret & 0x20) == 0);
	return ret;
}


/** @brief  Send a command byte to the tranceiver.
 *			Terminates the SPI transaction after one byte.
 *
 * @param[in]  cmd		Command byte.
 * @param[in]  wait		If nonzero wait for the command queue to be ready.
 * @return: The status word from the tranceiver chip.
 */
unsigned char adf_send_command (unsigned char cmd, unsigned char wait)
{
	unsigned char	ret;

	if (wait) {
		adf_wait_ready ();

		Nop ();		/* Take a short nap (so the CS pulse is visible on the scope). */
		Nop ();
		Nop ();
		Nop ();
		Nop ();
		Nop ();
		Nop ();
		Nop ();
		Nop ();
		Nop ();
	}

	/* Select the chip by lowering the CS pin. */
	ADF_CS = 0;

	/* Then wait for the SPI ready status bit to go high. */
	Nop ();
	Nop ();
	while (ADF_SDI == 0);

	/* Send the command byte. */
	SPI1BUF = cmd;

	/* Wait for the BufferFull bit to be set (end of transmission). */
	while (SPI1STATbits.SPIRBF == 0);
	ret = SPI1BUF;

	/* Wait for the clock bit to drop low again. */
	while (ADF_SCK == 1);

	/* Unselect the transceifer chip by raising the CS pin. */
	ADF_CS = 1;	

	return ret;			/* Return the status word. */
}


/** @brief  Write a byte to the memory space of the ADF chip.
 *			Terminates the SPI transaction afterwards.
 *
 * @param[in]  addr		Address of the memory location.
 * @param[in]  data		Data byte to write.
 * @return: The status word from the ADF chip.
 */
unsigned char adf_write_byte (unsigned int addr, unsigned char data)
{
	unsigned char	ret;

	/* Select the chip by lowering the CS pin. */
	ADF_CS = 0;

	/* Then wait for the SPI ready status bit to go high. */
	Nop ();
	Nop ();
	while (ADF_SDI == 0);

	/* Store the top byte of the address with bit 3 set as command. */
	SPI1BUF = 0x08 | (addr >> 8);

	/* Wait for the BufferFull bit to be set (end of transmission). */
	while (SPI1STATbits.SPIRBF == 0);
	ret = SPI1BUF;

	/* Store the lower byte of the address. */
	SPI1BUF = addr & 0xFF;

	/* Wait for the BufferFull bit to be set (end of transmission). */
	while (SPI1STATbits.SPIRBF == 0);
	ret = SPI1BUF;

	/* Store the data byte. */
	SPI1BUF = data;

	/* Wait for the BufferFull bit to be set (end of transmission). */
	while (SPI1STATbits.SPIRBF == 0);
	ret = SPI1BUF;

	/* Wait for the clock bit to drop low again. */
	while (ADF_SCK == 1);

	/* Unselect the transceifer chip by raising the CS pin. */
	ADF_CS = 1;	

	return ret;			/* Return the status word. */
}


/** @brief  Read a byte from the memory space of the ADF chip.
 *			Terminates the SPI transaction afterwards.
 *
 * @param[in]  addr		Address of the byte to fetch.
 * @return: The requested byte.
 */
static unsigned char adf_read_byte (unsigned int addr)
{
	unsigned char	ret;

	/* Select the chip by lowering the CS pin. */
	ADF_CS = 0;

	/* Then wait for the SPI ready status bit to go high. */
	Nop ();
	Nop ();
	while (ADF_SDI == 0);

	/* Store the top byte of the address with bit 3+4+5 set as command. */
	SPI1BUF = 0x38 | (addr >> 8);

	/* Wait for the BufferFull bit to be set (end of transmission). */
	while (SPI1STATbits.SPIRBF == 0);
	ret = SPI1BUF;

	/* Store the lower byte of the address. */
	SPI1BUF = addr & 0xFF;

	/* Wait for the BufferFull bit to be set (end of transmission). */
	while (SPI1STATbits.SPIRBF == 0);
	ret = SPI1BUF;

	/* Store a NOP byte (filler so the interface can prepare the output byte). */
	SPI1BUF = 0xFF;

	/* Wait for the BufferFull bit to be set (end of transmission). */
	while (SPI1STATbits.SPIRBF == 0);
	ret = SPI1BUF;

	/* Store a NOP byte (while retrieving the data byte). */
	SPI1BUF = 0xFF;

	/* Wait for the BufferFull bit to be set (end of transmission). */
	while (SPI1STATbits.SPIRBF == 0);
	ret = SPI1BUF;

	/* Wait for the clock bit to drop low again. */
	while (ADF_SCK == 1);

	/* Unselect the transceifer chip by raising the CS pin. */
	ADF_CS = 1;

	return ret;			/* Return the status word. */
}



/****************************************************************
*																*
*	Packet transmitter services.								*
*																*
****************************************************************/

/** @brief  Transmit buffer header definition.
 */
struct tx_header_block {
	struct {
		uint8_t		pending;		/* Handshake flag. True until transmitted. */
		uint16_t	length;			/* Length of packet incl header. */
	} control;

	struct {
		uint8_t		preamble [4];	/* Preamble bytes. */
		uint8_t		sync [4];		/* Sync bytes. */
	} data;
} __attribute__ ((packed));

/** @brief  Housekeeping telemetry block.
 */
struct tx_housekeeping_block {
	struct tx_header_block	header;

	/* Payload data. */
	uint8_t		payload [100];		/* Only short frames. */
} __attribute__ ((packed));


/** @brief  TX payload data block.
 */
struct tx_payload_block {
	struct tx_header_block	header;

	/* Payload data. */
	uint8_t		payload [600];
} __attribute__ ((packed));


/* Create a pair of tx_filler_block in the DMA memory space. */
struct tx_housekeeping_block tx_housekeeping_block [2]  __attribute__((space(dma)));
struct tx_housekeeping_block *current_tx_filler_block;

/* Create a pair of tx_payload_block buffers in the DMA memory space. */
struct tx_payload_block tx_payload_block [2]  __attribute__((space(dma)));

/* Create a dummy word in the DMA memory space for keeping the receiver happy. */
uint16_t	rx_dummy __attribute__((space(dma)));

/* Define hack to figure out the offset of the DMA memory space. */
#define DMA_BASE (((unsigned int)&rx_dummy) - __builtin_dmaoffset (&rx_dummy))

/* Holder of the next tx sequence value. */
uint8_t		tx_next_sequence_no;

/* Transmitter FIFO struct. */
struct tx_fifo {
	struct tx_header_block	*header;
};

/* Transmitter FIFO variables. */
#define TX_FIFO_LEN		8
uint8_t					tx_fifo_len = 0;
struct tx_fifo			tx_fifo [TX_FIFO_LEN];
struct tx_header_block	*tx_running = NULL;	/* Pointer to the currently transmitting block. */



/** @brief  Add a block to the tx_fifo.
 *
 * @param[in]  header	Pointer to the block header element.
 */
static void tx_fifo_add (struct tx_header_block *header)
{
	if (tx_fifo_len >= TX_FIFO_LEN) {
		return;		/* FIFO is full. Ignore the packet. */
	}

	header->control.pending = 1;			/* Set the pending flag. */
	tx_fifo [tx_fifo_len].header = header;
	tx_fifo_len++;
}



/****************************************************************
*																*
*	SPI2+DMA services - used for transferring data via the ADF.	*
*																*
****************************************************************/
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
int main (void) {
	int				x;
	unsigned int	ad_value;

	/* Configure oscillator. */
	CLKDIVbits.FRCDIV  = C_FRCDIV_;
	CLKDIVbits.PLLPRE  = C_PLLPRE_;
	CLKDIVbits.PLLPOST = C_PLLPOST_;
//	CLKDIVbits.DOZE    = C_DOZE_;
	PLLFBDbits.PLLDIV  = C_PLLDIV_;


	/* Map PPS pins to their propper devices. */
	// Unlock the control registers.

	/* Pin mappings for SPI port 1 connected to the ADF control port. */
	RPOR0bits.RP0R = 0x07;		/* RP0  <= SDO1		ADF MOSI pin. */
	RPOR0bits.RP1R = 0x08;		/* RP1  <= SCK1		ADF SCLK pin.*/
	RPINR20bits.SCK1R = 1;		/* RP1  => SCK1:in	--//-- */
	RPINR20bits.SDI1R = 2;		/* RP2  => SDI1		ADF MISO pin. */

	/* Pin mappings for SPI port 2 connected to the ADF SPORT data port. */
	RPINR22bits.SCK2R = 3;		/* RP3  => SCK2:in	ADF SPORT CLK pin. */
	RPOR2bits.RP4R = 0x0A;		/* RP4  <= SDO2		ADF SPORT DT pin. */
	RPINR22bits.SDI2R = 5;		/* RP5  => SDI2		ADF SPORT DR pin. */

	/* Pin mappings for UART port 1 connected to the world. */
#if HWVERSION == 11
	RPOR3bits.RP6R = 3;			/* RP6  <= TX1		Serial link 1. */
	RPINR18bits.U1RXR = 7;		/* RP7  => RX1		Serial link 1. */
#elif HWVERSION == 10
	RPOR4bits.RP8R = 3;			/* RP8  <= TX1		Serial link 1. */
	RPINR18bits.U1RXR = 9;		/* RP9  => RX1		Serial link 1. */
#endif

	/* Pin mappings for UART port 2 connected to the world. */
	RPOR6bits.RP12R = 5;		/* RP12 <= TX2		Serial link 2. */
	RPINR19bits.U2RXR = 13;		/* RP13 => RX2		Serial link 2. */

	// Lock the PPS control again.

	/* Configure hardware ports. */	
	LED_1_TRIS = 0;		/* Make it an output port. */
	LED_2_TRIS = 0;		/* Make it an output port. */

	/* Read the hardware ID value from the debug pins. */
	id_no = (PORTB >> 10) & 0x03;
	Nop ();
	Nop ();

	init_timer1 ();		/* Configure Timer-1 to produce 10 interrupts per second. */
	init_adc ();		/* Initialize AD converter. */

	/* Init overall interrupts. */
	INTCON1bits.NSTDIS = 0;		/* Nesting is enabled. */
	SRbits.IPL = 0;

#if 0
	/* Read the ADC value a number of times to get the battery voltage. */
	for (x = 0; x < 3; x++) {
		while (!update_flag) {
			Nop ();		/* Wait for the update flag before continuing. */
		}
		update_flag = 0;

		/* Start the ADC for the next conversion. */
		AD1CON1bits.SAMP = 0;

		/* Wait for the ADC sample to be ready. */
		while (AD1CON1bits.DONE == 0) {
			Nop ();
		}
		ad_value = ADC1BUF0;
	}
	if (ad_value >= 0x08BC) {
		pa_enable = 1;			/* Above 12.0 volt. On battery charger. Disable PA. */
	}
#endif

	/* Initialize the tx_filler_block headers. */
	housekeeping_reset ();
	prepare_packet (&tx_housekeeping_block [0].header, id_no, sizeof (housekeeping_telemetry), housekeeping_get_byte);
	housekeeping_reset ();
	prepare_packet (&tx_housekeeping_block [1].header, id_no, sizeof (housekeeping_telemetry), housekeeping_get_byte);
	current_tx_filler_block = &tx_housekeeping_block [0];

	/* Clear the pending flag in the tx_payload_block elements. */
	tx_payload_block [0].header.control.pending = 0;
	tx_payload_block [1].header.control.pending = 0;

	switch (id_no) {
		case 0:	pa_level = 0xB1;
				// pa_enable = 0;	/* PA enable is controlled by battery voltage. */
				break;
		case 1:	pa_level = 0xC1;
				// pa_enable = 0;	/* PA enable is controlled by battery voltage. */
				break;
		case 2:	pa_level = 0xB1;
				pa_enable = 1;			/* Force disable the PA module. */
				break;
		case 3:	pa_level = 0xC1;
				pa_enable = 1;			/* Force disable the PA module. */
				break;
	}
	Nop ();
	Nop ();

	/* Start the ADF transmitter. */
	init_spi1 ();		/* Init SPI1 for talking to the ADF. */

	switch (id_no) {
		case 0:
		case 2:	adf_init (0x00039000, 2500, 0);
				break;
		case 1:
		case 3: adf_init (0x00039000 + (2000000/10000), 2500, 0);
				break;
	}

	/* Initialize the SPI2 and DMA support for transmitting data. */
	init_spi2_dma ();

	/* Initialize the two serial ports. */
	init_rx1 ();
	init_rx2 ();


	/* Turn on the transmitter and let things onfold from here. */
	adf_cmd_phy_on ();
	adf_cmd_phy_tx ();


#if HWVERSION == 11
	/* Enable the PA block. */
	PA_EN = pa_enable;
	PA_EN_TRIS = 0;
#endif


	/* Main loop - waiting for certain events. */
	while (1) {
		struct tx_payload_block *txp_ready = NULL;

		/* Find a empty tx_payload block. */
		if (tx_payload_block [0].header.control.pending == 0) {
			txp_ready = &tx_payload_block [0];
		} else if (tx_payload_block [1].header.control.pending == 0) {
			txp_ready = &tx_payload_block [1];
		}

		if (txp_ready != NULL) {
			/* Found it. Find some data for it. */
			if (RING_PACKET_LEN (rx1) > 0) {
				/* Fetch a packet from rx1 and put it into txp_ready. */
				unsigned int	len;

				LED_2 ^= 1;		/* Toggle debug LED. */

				len = rx1_get_byte ();			/* The header byte is the length. */
				prepare_packet (&txp_ready->header, 0x11, len, rx1_get_byte);

				/* Enqueue this new block so it gets transmitted. */
				tx_fifo_add (&txp_ready->header);
			}
			else if (RING_PACKET_LEN (rx2) > 0) {
				/* Fetch a packet from rx2 and put it into txp. */
				unsigned int	len;

				LED_1 ^= 1;		/* Toggle debug LED. */

				len = rx2_get_byte ();			/* The header byte is the length. */
				prepare_packet (&txp_ready->header, 0x12, len, rx2_get_byte);

				/* Enqueue this new block so it gets transmitted. */
				tx_fifo_add (&txp_ready->header);
			}
		}


		if (update_flag) {
			/* Set by the timer1 interrupt function 10 times per second. */
			update_flag = 0;

			/* Update the tx_filler_block with new data. */
			if (current_tx_filler_block == &tx_housekeeping_block [0]) {
				/* Update block [1] as block [0] is being used. */
				housekeeping_reset ();
				prepare_packet (&tx_housekeeping_block [1].header, id_no, sizeof (housekeeping_telemetry), housekeeping_get_byte);

				/* Enqueue this new block so it gets transmitted. */
				tx_fifo_add (&tx_housekeeping_block [1].header);

				/* It is now the new filler block. */
				current_tx_filler_block = &tx_housekeeping_block [1];
			} else {
				/* Update block [0] as block [1] is being used. */
				housekeeping_reset ();
				prepare_packet (&tx_housekeeping_block [0].header, id_no, sizeof (housekeeping_telemetry), housekeeping_get_byte);

				/* Enqueue this new block so it gets transmitted. */
				tx_fifo_add (&tx_housekeeping_block [0].header);

				/* It is now the new filler block. */
				current_tx_filler_block = &tx_housekeeping_block [0];
			}

			/* Start the ADC for the next conversion. */
			AD1CON1bits.SAMP = 0;
		}

		switch (debug) {
			case 0: break;

			default:
				adf_set_pa_level (debug);
				debug = 0;
				break;
		}
	}
}

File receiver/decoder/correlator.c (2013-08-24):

/* -*- c -*- */
/*
 * Copyright (c) 2013 Peter Scott, OZ2ABA
 *
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
 * You should have received a copy of the GNU General Public License
 * along with strx; see the file COPYING.  If not, write to
 * the Free Software Foundation, Inc., 51 Franklin Street,
 * Boston, MA 02110-1301, USA.
 */
#include <stdio.h>
#include <stdlib.h>
#include <stdint.h>
#include <unistd.h>
#include <string.h>
#include <errno.h>
#include <time.h>
#include <signal.h>
#include <fcntl.h>

#include <sys/types.h>
#include <sys/socket.h>
#include <sys/time.h>
#include <netinet/in.h>
#include <sys/socket.h>
#include <arpa/inet.h>

#include "viterbi.h"

/** @brief Trellis encoder table.
 */
uint8_t trellis_encoder [0x8000];


typedef enum {INIT, HUNT, COLLECT_HEAD, COLLECT_ALL} state_t;

typedef struct _correlator_t {
	state_t		state;			/* Engine state. */
	uint32_t	sr;			/* Shift register for asembling bytes. */
	uint32_t	flag;			/* Flag value. */

	unsigned int	sampleno;		/* Number of samples collected. */
	unsigned int	total_samples;		/* Total number of samples to collect for the full packet. */

	uint8_t		packet_buf [1024];	/* Byte buffer array for the decoded data. */
	unsigned int	packet_len;		/* Length of the packet in the buffer. */
	unsigned int	pbit;
	unsigned int	flag_err;		/* Number of error bits in flag. */
	unsigned int	trellis_err;		/* Number of error bits corrected by the Trellis encoding. */

	struct v	*vp;			/* Viterbi instance. */
	COMPUTETYPE	*symbols;		/* Pointer to a symbol buffer for the Viterbi decoder. */
	uint8_t		raw_buf [2048];		/* Buffer for storing the raw packet in packed format (for trellis check). */
} correlator_t;


fd_set	fixed_read_fds;
int	fixed_nfds;

struct client {
	struct client	*prev;	/* Pointer to the previous one in the chain. */
	struct client	*next;	/* Pointer to the next one in the chain. */
	int		fd;	/* Socket file descriptor. */
};

struct client_set {
	int			listen_fd;	/* Accept socket. */
	unsigned long long	packets;	/* Number of packets received on this channel. */
	unsigned long long	bytes;		/* Number of bytes received on this channel. */
	struct client		*list;		/* List of connected sockets. */
};

struct client_set client_set [270];	/* Array of client sockets. */

uint8_t	last_housekeeping [100];	/* Buffer to hold the last received housekeeping packet. */

/* Macro to insert a entry into a list. */
#define INSERT_INTO_LIST(list,element) do { \
	element->next = list; \
	if (element->next) element->next->prev = element; \
	list = element; \
} while (0)

/* Macro to remove a entry from a list. */
#define REMOVE_FROM_LIST(list,element) do { \
	if (element->prev == NULL) {	/* First element in the list. */ \
		list = element->next; \
		if (element->next) element->next->prev = NULL; \
	} else {	/* Not the first element. */ \
		element->prev->next = element->next; \
		if (element->next) element->next->prev = element->prev; \
	} \
} while (0)



static void init_sockets (void)
{
	int			x;
	struct sockaddr_in	addr;
	size_t			addr_size;
	int			opt_val;

	memset (client_set, 0, sizeof (client_set));
	FD_ZERO (&fixed_read_fds);
	fixed_nfds = 0;

	/* Create a listening socket for the first 32 slots. */
	for (x = 0; x < 32; x++) {
		client_set [x].listen_fd = socket (AF_INET, SOCK_STREAM, 0);
		if (client_set [x].listen_fd < 0) {
			perror ("socket: ");
			exit (1);
		}

		opt_val = 1;
		setsockopt (client_set [x].listen_fd, SOL_SOCKET, SO_REUSEADDR, &opt_val, sizeof (opt_val));

		addr.sin_addr.s_addr = INADDR_ANY;
		addr.sin_port = htons (4000 + x);
		addr.sin_family = AF_INET;
		addr_size = sizeof (addr);
		if (bind (client_set [x].listen_fd, (struct sockaddr *)&addr, addr_size) < 0) {
			perror ("bind: ");
			exit (1);
		}

		if (listen (client_set [x].listen_fd, 5) < 0) {
			perror ("listen: ");
			exit (1);
		}

		/* Add the listening handle to the fixed read_fds. */
		FD_SET (client_set [x].listen_fd, &fixed_read_fds);
		if (client_set [x].listen_fd >= fixed_nfds) {
			fixed_nfds = client_set [x].listen_fd + 1;
		}
	}

	/* Create a listening socket for the command port. */
	client_set [260].listen_fd = socket (AF_INET, SOCK_STREAM, 0);
	if (client_set [x].listen_fd < 0) {
		perror ("socket: ");
		exit (1);
	}

	opt_val = 1;
	setsockopt (client_set [260].listen_fd, SOL_SOCKET, SO_REUSEADDR, &opt_val, sizeof (opt_val));

	addr.sin_addr.s_addr = INADDR_ANY;
	addr.sin_port = htons (5000);
	addr.sin_family = AF_INET;
	addr_size = sizeof (addr);
	if (bind (client_set [260].listen_fd, (struct sockaddr *)&addr, addr_size) < 0) {
		perror ("bind: ");
		exit (1);
	}

	if (listen (client_set [260].listen_fd, 5) < 0) {
		perror ("listen: ");
		exit (1);
	}

	/* Add the listening handle to the fixed read_fds. */
	FD_SET (client_set [260].listen_fd, &fixed_read_fds);
	if (client_set [260].listen_fd >= fixed_nfds) {
		fixed_nfds = client_set [260].listen_fd + 1;
	}
}


static int dump_telemetry (int fd)
{
	char		buf [10000];
	char		*bc = buf;
	uint32_t	upt = last_housekeeping [1] + (last_housekeeping [2] << 8) + (last_housekeeping [3] << 16) + (last_housekeeping [4] << 24);
	float		vbat = ((24.9+4.7)/4.7) * (last_housekeeping [5] + (last_housekeeping [6] << 8)) * (3.3 / 4095.0);
	int		x;

	/* Forst dump some info from the housekeeping block. */
	bc += sprintf (bc, "TX: %d  Uptime: %d.%d  Vbat: %5.2f  Flags: %04X",
			   last_housekeeping [0],
			   upt / 10, upt % 10,
			   vbat,
			   last_housekeeping [7] + (last_housekeeping [8] << 8));

	for (x = 0; x < 256; x++) {
		if (client_set [x].packets > 0) {
			bc += sprintf (bc, "\t%d:%llu,%llu", x, client_set [x].packets, client_set [x].bytes);
		}
	}
	bc += sprintf (bc, "\n");

	return send (fd, buf, (bc - buf), MSG_NOSIGNAL);
}
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

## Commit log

2013-03-28 strx: Switch to gnuradio-runtime.
2013-03-29 strx: Add option foir input device or file and prepare for UHD source.
2013-03-29 strx: Add support for selecting USRP antenna.
2013-03-31 strx: Switch new namespace-style coding.
2013-04-13 strx: Replace FFT filter with translating FIR filter.
2013-04-13 strx: Export the filter offset setting to control port.
2013-04-27 strx: Include FFT block in flowgraph (issue #1).
2013-05-02 strx: FFT thread framework.
2013-05-04 strx: Stick to plain floats in FFT chain.
2013-05-05 strx-mon: functional framework for fetching LO and FFT via control port.
2013-05-05 strx-mon: Update FFT plot at 10 Hz (issue #1).
2013-05-07 strx: Switch to 4 MHz bandsidth.
2013-05-07 strx-mon: Switch to 4 MHz bandsidth.
2013-05-10 strx: Make filter cutoff available to clients.
2013-05-10 strx-mon: Update filter offset at 1 Hz.
2013-05-10 strx-mon: Update Center frequency at 1 Hz.
2013-05-10 strx-mon: Update filter cutoff at 1 Hz.
2013-05-10 strx-mon: Add button for swapping the channels.
2013-05-10 strx-mon: Control filter offset from gui.
2013-05-10 strx-mon: Implement record button functionality.
2013-05-10 strx-mon: Trigger UI update when channel is swapped.
    We reset the callback counter every time the CHAN button
    is pressed. This will force an update the next time the
    callback is executed.
2013-05-10 strx-mon: Implement filter cutoff control.
2013-05-10 strx-mon: Only update filter offset if new value is different from old one.
2013-05-12 decoder: Updated correlator with statistics (broken).
    [correlator.c]
2013-05-12 Revert "decoder: Updated correlator with statistics (broken)."
    This reverts commit 325bda3600f257d0921a87879b33643ee5bafeae.
    [correlator.c]
2013-05-12 strx: First cut at snr to frequency converter.
2013-05-12 strx: Create audio feedback and increase FFT rate to 100 Hz (issue #3).
2013-05-14 decoder: Fixed correlator with statistics.
    [correlator.c]
2013-05-15 strx: Lower FFT and SNR processing frequency to 25 Hz.
2013-05-18 strx-mon: Use correct application name in file headers.
    [main.cpp]
2013-05-18 strx-mon: Extract TX volt and uptime from statistics.
2013-05-18 strx-mon: Fix TX status regexp and update battery voltage in gui.
2013-05-29 strx-mon: Use correct hostname for statistics server.
    [main.cpp]
2013-05-29 strx-mon: Switch to QTime based statistics update.
2013-08-14 TX board v1.0
    [sapphire_tx_board.brd, sapphire_tx_board.sch]
2013-08-14 TX board v1.1
    [sapphire_tx_board.brd, sapphire_tx_board.sch]
2013-08-14 TX board v1.1a
    [sapphire_tx_board.brd, sapphire_tx_board.sch]
2013-08-24 decoder: Use correct aplication name.
    [correlator.c]
2013-08-30 doc: Added diagram of receiver chain.
2013-08-30 doc: Added simplified USRP1 RX chain diagram.

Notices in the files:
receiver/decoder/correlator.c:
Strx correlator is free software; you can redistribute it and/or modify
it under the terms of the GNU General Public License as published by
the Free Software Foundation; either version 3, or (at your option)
